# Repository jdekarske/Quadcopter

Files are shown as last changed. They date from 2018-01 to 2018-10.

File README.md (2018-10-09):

<<<<<<< HEAD
# README #

What a machine!

This REPO demonstrates the BADGER Lab's Motion Capture system applied to a 450mm quadcopter. The main interest to the lab is the integration of Optitrack Motive with MatLab. See the [documentation](https://v20.wiki.optitrack.com/index.php?title=Data_Streaming) for instruction on set-up. Download the NatNet SDK for use with MatLab. It should be set up on the lab computer, but I'm not sure if it applies to all user partitions. A MatLab example comes with the SDK.

## Quadcopter Usage
* Calibrate cameras liberally; ensure flight volume is thoroughly wanded and you receive an "exceptional" grade in all categories.
* Establish ground plane with the northwest corner of the forceplate.
* Line the quadcopter struts **EXACTLY** with the north end of the forceplate, motor one faces south.
* On GUI: ensure the rigid body moves with the correct axes, Frames per second match camera rate, abort button is greyed
* Start flight from hand, click motors on. Guide for a few seconds while the integral term catches up.

## Key Streaming Excerpts
* Initialize any variables under `function QuadcontrolV2_OpeningFcn(hObject, eventdata, handles, varargin)`
* The critical code comes from the initialization. Specify `addlistener( [rigidbody (probably '1')], [callback function])`.
```
c = natnet;
c.ConnectionType = 'Multicast';
c.connect
c.addlistener( 1 , 'ControlCallbackV2' );
```
* To grab position data in the callback, use the evnt structure. (Goodluck with the axes)
```
rbx = -double( evnt.data.RigidBodies( rbnum ).y );`
```
* Be sure to add buttons for `c.enable(0)` and `c.disable(0)` otherwise the script will not terminate and you will have to kill matlab via task manager and you'll be unhappy because you forget to do it properly after writing sticky notes to remind yourself.
* Use [set](https://www.mathworks.com/help/matlab/ref/set.html) and [drawnow](https://www.mathworks.com/help/matlab/ref/drawnow.html) functions for easy plotting and GUI stuff! *update: Don't use gui stuff while flying!! it adds significant computing time*

### Who should you contact when nothing works and is poorly commented?
[jdekarske@wisc.edu](mailto:jdekarske@wisc.edu?subject=Your%20code%20sucks)

*UW BADGER Lab 1/25/2018*
=======
# Quadcopter
Open-source flight controller software based on Optitrack position tracking
>>>>>>> Github/master

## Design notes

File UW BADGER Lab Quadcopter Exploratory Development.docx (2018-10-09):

# UW BADGER Lab Quadcopter Exploratory Development

Prepared by: Jason Dekarske 6/28/2018

# Abstract

A quadcopter is a study of the challenge of digital controls and its demand for well understood physics. Each component must work together flawlessly, or the consequences could be catastrophic. The goal of this project was to construct a custom 4 rotor robot capable of following high level commands from a command station using position input from the BADGER Lab’s motion capture system. The motivation is to create a testbed for student development in ME 349: Introduction to Robotics. We sourced inexpensive parts with the intention of creating more than one unit for the use in the course and to control for broken devices. This document outlines the progress made toward this goal and the things the author has learned.

# Note

This writing is organized by quad theory, then component functional discovery and finally system integration and theory. It is important to note that most components may not be available exactly as described, but it should be possible to find a clone for similar price range. With that said, the greatest difficulty was sidestepping physical properties of components, as documentation was scarce, and proceeding with experimentation and trial and error. Hopefully the strategies laid out are helpful in recreating a functional device in the case an exact replacement cannot be found.

# Wait, this thing flies?

There are many examples in literature that outline quadcopter function at the PhD level with formality that is not necessarily important to get this thing in the air. Alternatively, hobby documentation of open source flight computers cannot be made to meld with the unique setup in the BADGER Lab. This is precisely the challenge presented here. Where quadcopter research labs have thousands to produce a robust, acrobatic system (see: coding and algorithms), an introductory course that spends a small unit on flight cannot compete. This will be touched later in design criteria and some choices of subsystems.

With basic understanding of Newton’s laws, we can construct a working device that will (hopefully) not destroy itself. From this base we can add toppings that improve the flavor and robustness to the system. Every write-up on quadcopters must include a form of the following nifty graphic (Figure 1). Notice the body frame is attached in line with the rotors. This simplifies the math greatly, since a movement in one direction is only dependent on one axis. Additionally, adjacent rotors spin in opposite directions to cancel torque; we will abuse this later.

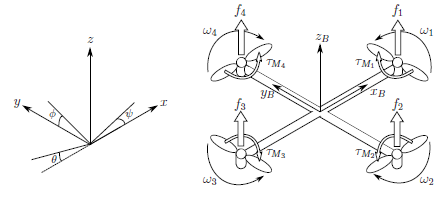
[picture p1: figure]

Let’s get some equations rolling. First, we will model the quadcopter attached to a vertical pole: controlling only its altitude (Excuse my janky powerpoint shape free body diagrams please).

M1,M2

M3,M4

mg

x

θ

After accepting the brutal truth that we will not have a perfectly stable quadcopter we would find it’s thrust to be the following:

T=∑ F_(Mi) *cosθ*cosφ-m*g

This means to accelerate up or down, we should modulate the force of the motors equally. Note the cosine terms include the angular correction for both horizontal axes. Not so tough, let’s look at keeping it stabilized. This time, we attach one axis to a horizontal pole (I actually did this, see later)

M1

M3

x

θ

In this plane, we are only looking at the rotational dynamics between opposite motors. We find the angular acceleration where I is the inertia of each axis and L is the length motor to motor (450mm):

I*θ=L/2(F_(M3) -F_(M1) )

I*φ=L/2(F_(M4) -F_(M2) )

Finally, we consider the final axis of the quadcopter: the yaw. Following a similar strategy, let’s only compare the relative forces of the motors.

M4

M2

M3

M1

As is the theme of this project, I was given no details of the physical properties of the propellers, so we need to take this part off-road a bit. We have intuition that rotating the M1,M3 pair faster than M2,M4 would result in the quad rotating clockwise (or negative Ψ) due to Newton’s second Law. If we assume the propellors are the same and everything is symmetrical, I conjecture:

IΨ=(F_(M2) +F_(M4) )-(F_(M1) +F_(M3) )

In the coming sections we will revisit how these physical relations can be put into code!

# I am in control!

Okay, so I’ve been pretty blunt about our lack of knowledge about our system. Surprise! Our engineering project isn’t ideal. The saving grace will be our controller, something that takes feedback from our sensors and adjusts accordingly. We’ll be using the popular PID scheme to correct errors. This requires an input, the motors, and an output, the position. This comes in two layers: stabilization and movement. Our inner layer, stabilization is priority number one. If we can keep the quadcopter stable, it ain’t goin nowhere. So, as our input, we command the angular position to be 0° for all axes. The controller will modulate the motors, as an output, to achieve this position with the help of the equations we developed earlier. Next, our outer later. Say we want to move our quadcopter 2 meters North (+y). Let’s command an angle ϕ = 2° and decrease to zero. This results in the quadcopter banking toward the north and stopping at 2 meters North. This all sounds good in theory, but let’s apply it.

I glossed over a crucial part of control in the last paragraph: PID. It stands for Proportional Integral Derivative, the three operations used in the algorithm. I’ll attack this in words and intuition first and equations after, feel free to switch between as you wish. These all work as a function of error, or the difference between the current input and the commanded input: e=z_0 -z , for example, where z is the height of the quadcopter and z_0 is our desired height of the quadcopter. Looking at the proportional term, it will take the error and multiply it by a “gain”, often k_p , and spit out an output, let’s say thrust. So, if we’re z=1 and want to be z_0 =3 , with k_p =2, T=2*(3-1)=4 . Our output thrust is 4 which commands the motors to spin faster and ascend. A little hand-wavy, I know, we will get to how “thrust” interacts with the motors. As the quad approaches our desired height, the error will decrease and thus, the thrust. However, if the quad is moving too fast as it gets to the desired path it may overshoot! We are higher than the desired point and the thrust goes negative, and the motors slow down to descend. Let’s fix this with the Derivative term. As the name implies, we take the derivative of the error, (de)/(dt) , so we need to factor in a time variable. Since a computer is doing this math, we’ll have discrete sample points to calculate the error and time between each sample, perfect! Let’s find the difference in error between now and the last sample and divide by the time it took. How does this help us? If we are approaching our desired height too fast we will notice a large negative derivative term, because the error is decreasing quickly. We multiply this by a term k_d and add it to the output. This decreases the output as we approach our desired point. Finally, we have the Integral term which is used for fixing steady state errors. The motors we have are quite sensitive, to stay within a ~cm of our setpoint, we need a low proportional term, or it will oscillate over and under the desired point. This is okay, but if the quad is very low, the term may not raise the output high enough to get to the desired point: a steady-state error. The integral term, as expected integrates, or adds, consecutive error between samples multiplies by the time between samples and you guessed it, k_I , and tacks it on to the output. In summary, P fixes error, I keeps P under control, and I fixes outstanding error. That was a lot, let’s put it in maths and grapths.

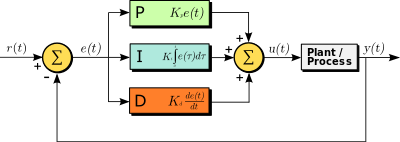
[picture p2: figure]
Image result for pid controller

Here we see the three familiar terms in the middle and a bunch of arrows pointing everywhere. r(t) is our desired point which stays the same, the summation circle subtracts the output, y(t) to give e(t), the error. Then, the PID terms do their thing and sum at the next circle to give our command to the motors, u(t). The motors move the quad, plant, and give us an output, position. Here are some examples of controllers with different gain values and how they interact. Note how red doesn’t overshoot, but it takes longer to reach the reference signal. These are the balances that must be made. Later we will work on finding what gains to use or “tuning”, this was the bulk of the time spent on the project.

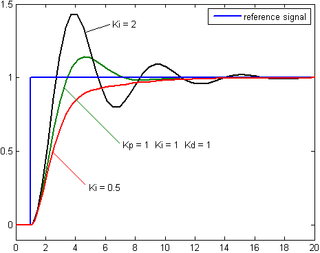
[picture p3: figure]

# Design criteria

Because this was meant for a near graduate level course, it’s important to make the system accessible for tinkering and experimentation in the scope of robotics. The following criteria are in no way absolute for professional, experimental, or hobby quadcopter design. Starting with the tinkering theme, we need a microcontroller that can talk to the motion tracking system and the motors: an Arduino is a cheap solution that is very easy to use. Next, a large quad can claim slower dynamics by its increased mass and rotational inertia. Additionally, a larger footprint gives us a larger margin of error for the tracking markers because they can be placed further apart. Human sized wouldn’t fit in the lab so we’ll go with a small dog sized craft. Typically, these come in the flavor of a 450mm wingspan and a kilo or two. Consequently, we’ll need bigger motors powered by a bigger battery. Finally, we need communication between all our systems. I would have liked to use wifi for everything, but IT has the building on lockdown for router paraphernalia. We’ll make our own radio signals with a common 2.4GHz RF transceiver (it’s faster than wifi anyway!). I’ll breakdown each component in the following subsections.

## Frame

Let’s start with the part that looks pretty and holds things together. It took two iterations before I decided to use a tried and true frame. The first was some plexiglass screwed together in a not so balanced way, so I could get a feeling for where the components could go. Initially, I chose an “H” configuration. This setup allowed me to use the full length of the board for mounting and routing wires. This came at a cost of added weight and asymmetrical inertias. I was embarrassed by my poor craftsmanship, so I moved on to round two.

From a salvaged plexiglass sheet found in the design scraps, (SE corner ECB basement, seriously, go there, it’s a goldmine) I laser cut a beautiful four-piece frame with splines and everything. It was taller and had a two-tier mounting area. The lower tier contained the battery to lower the center of gravity while the upper tier held the controller. This time I went with the “X” configuration. I figured that if I didn’t assign which way was forward, it’s easier to play coy when it doesn’t cooperate. Also, having a single motor assigned to each axis with similar inertias makes the math much easier. Finally, since I was constructing a 3-dimensional device from 2-dimensional pieces, having perpendicular intersections made fitting the pieces easier. My beautiful artwork met its fate when a motor failed, and it dive bombed the hardened concrete floor. Tears were shed, but it was best I moved on to something guaranteed by Amazon to work.

Here is the “RipaFire®” 450 frame that I found on Amazon that is surprisingly still sold more than a year later. It is even made of “advanced engineering material”! I chose this in particular because it had a built in power distribution board. The bottom part of the frame is actually a PCB which routes power from the battery to the ESC’s (covered later). This saves me an extra part and consolidates wires, always a plus. Additionally, the motors fit the standard holes at the ends, the battery can fit in the lower portion, and I have plenty of room for a microcontroller on top.

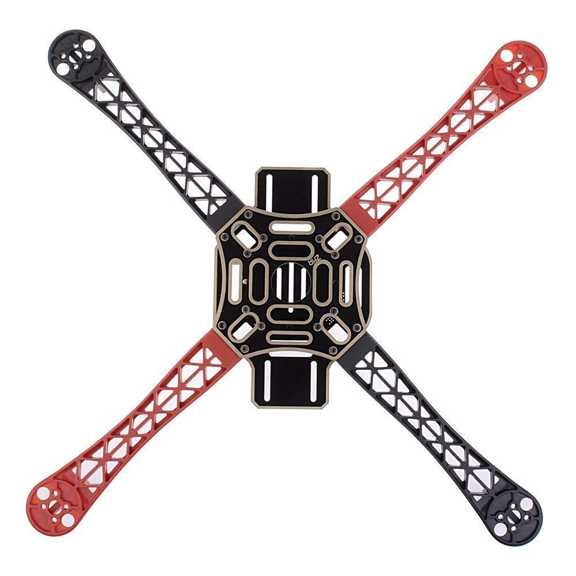
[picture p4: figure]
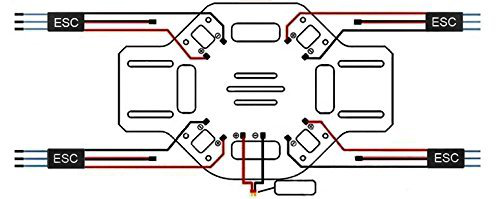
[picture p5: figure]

## Motors

On to the star players! This is what really drove the decision making for the other components. Without a huge background in aeronautics, I was stumped for what to choose. I had to stay away from quality genuine motors to save the budget so generic ones from AliExpress had to do. I scoured forums of custom builds to see what parameters were typical for a quad of my size. I settled on a 920KV brushless motor. KV is the velocity constant of the motor – thousand RPM/Volt. https://oscarliang.com/quadcopter-motor-propeller/ Generally, lower RPMs are suitable for larger propellers and quads. Since we have a rather large craft, I dutifully followed the table and stayed under 1000KV. When connecting to the ESC, the wires can connect in any combination; if the motor spins the wrong way, switch two of them.

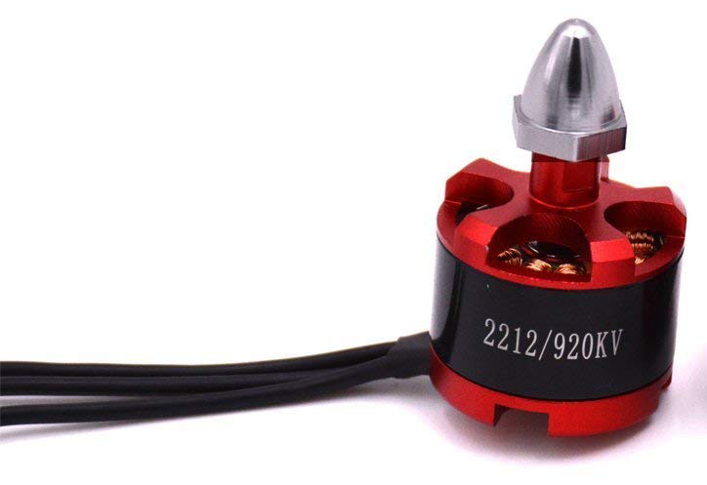
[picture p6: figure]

## Propeller

I’m not sure this deserves a section with how little I spent researching. In hindsight, one of the most critical features did not see that much love. They certainly showed their displeasure by providing several casualties to my defenseless fingers. Following the table from above, I used a 1045 propellor which means 10” diameter and 45° pitch. I ordered a few packs figuring these would break often, I was, unfortunately, very correct. We visited the direction these should spin earlier, double check, as these are directional.

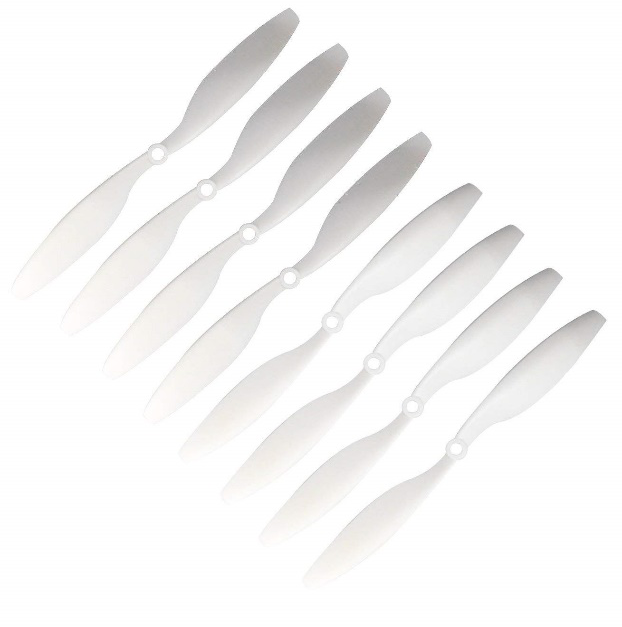
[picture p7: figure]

## Electronic Speed Controllers

What moves the motor you might ask? These convenient, drop and go, boards take PWM input from the controller and 12V from the battery, and transform to 3 phase output for the motors! Gorgeous! They just need a little programming. Most run with a standard firmware that is easy to change with an RC controller and a datasheet. The beauty of minimum spec designs meant I had neither! Fortunately, I could emulate a controller with the Arduino and after much experimentation with similar looking boards, I found a datasheet that kind of worked (See setup for details). The important parameter was finding an ESC with a high enough current rating. The only downside to choosing one with a higher rating meant a heavier piece. In this case, the weight of the ESC is negligible, so I went with a conservative 30A (compared to similar builds). Amazon gave me what I needed and a few extra after they burned out. I eventually found some that will cut the power if the motor stalls after getting the propellers caught under a desk. This and other features will be explored later. Note the extra is the output of the battery elimination circuit (BEC) which powers our microcontroller with a nice 5V.

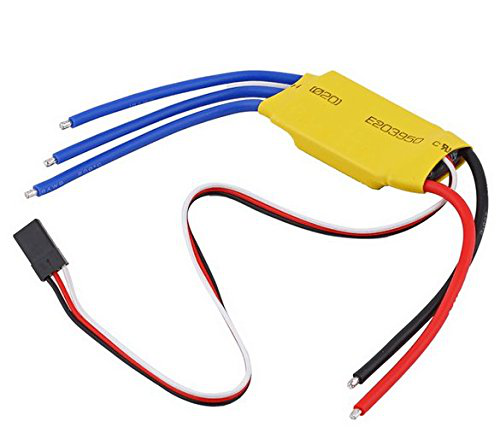
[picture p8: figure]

## Battery

Going down the line we see the heaviest chunk in the mix. The 4 cell LiPo was chosen based on reviews from Amazon and requirements for the motors capabilities. Out of all the parts, this is potentially the most dangerous. Starting Peter’s lab on fire was pretty high on the list of “do not’s”. I also grabbed a charger with a balancing feature. It’s crucial to note the cells should not be discharged lower than 3V. I tested the battery before and after sessions and when it was clear the motors weren’t working as hard as usual. The battery needed a discharge rate that would match our use. The “C” rating determines the nominal current available. With a 2.2 Ah capacity and 25C rating, our available current is 2.2*25 = 55A. This means it should be tough to burn out our ESC’s at full power when the current is distributed to four motors.

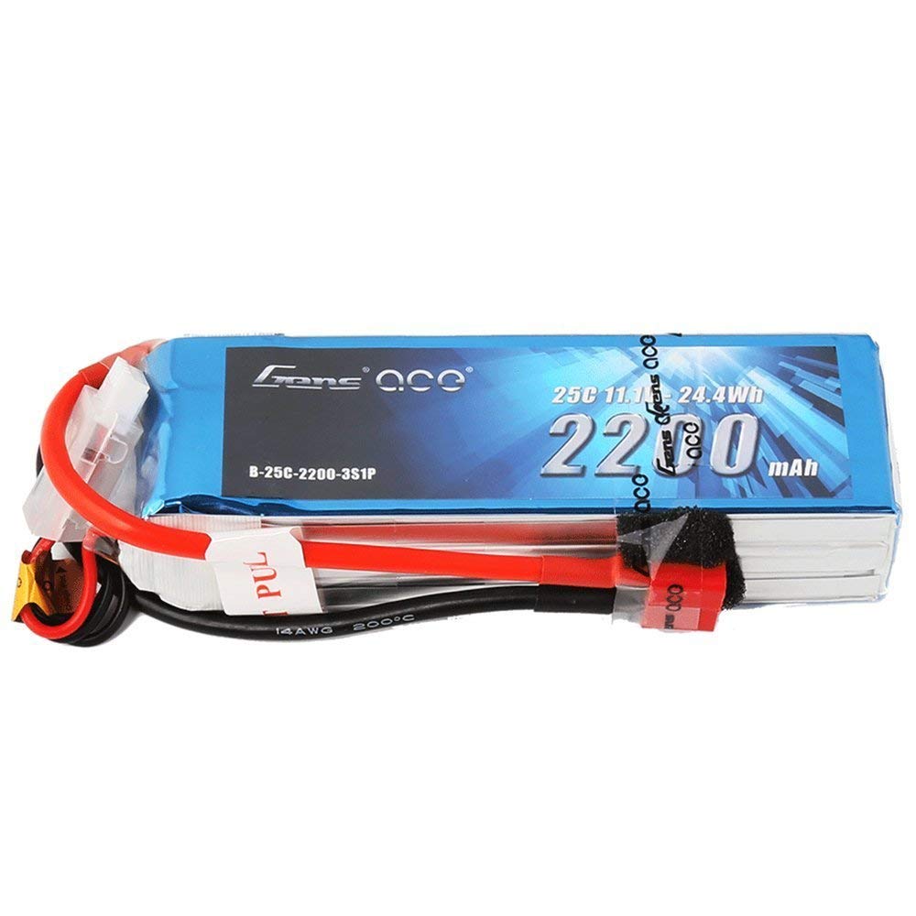
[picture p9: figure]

## Microcontroller

Being well versed in the language of DIY made this an easy choice. I needed 4 PWM channels, serial, SPI and I²C support, 5V power, and be on the small side. I already used an Arduino in tandem with the NRF24L01 (next section!) so implementation would be quick, or so I thought. I went with a clone of an Arduino Nano, fairly small, and it hits all the requirements.

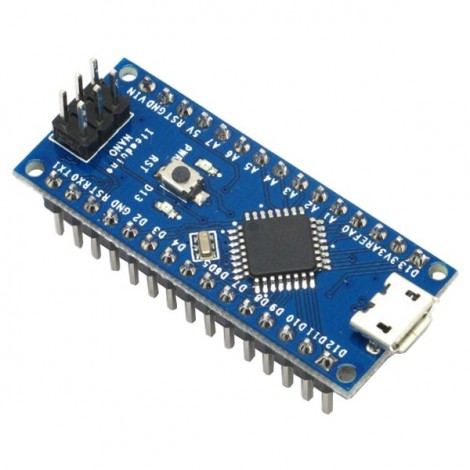
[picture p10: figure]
Image result for arduino nano clone

## RF Transceiver

This choice was part necessity, part personal preference. Like I said before, I knew wifi communication would be a battle I didn’t want to fight with IT so I sprung for the next best option. The NRF24L01 is a popular chip used by many hobbyists because of an extremely well documented and supported library for Arduino. I could have chosen Bluetooth, which is similar but I didn’t need to worry about acknowledgements or connection testing, so I threw that all out. I could easily send a string to be parsed on the other side with a simple function. The commands moved so fast, it wasn’t worth checking if they got there as a new command was already on its way. The only modification was a 47 uf decoupling capacitor soldered between power and ground.

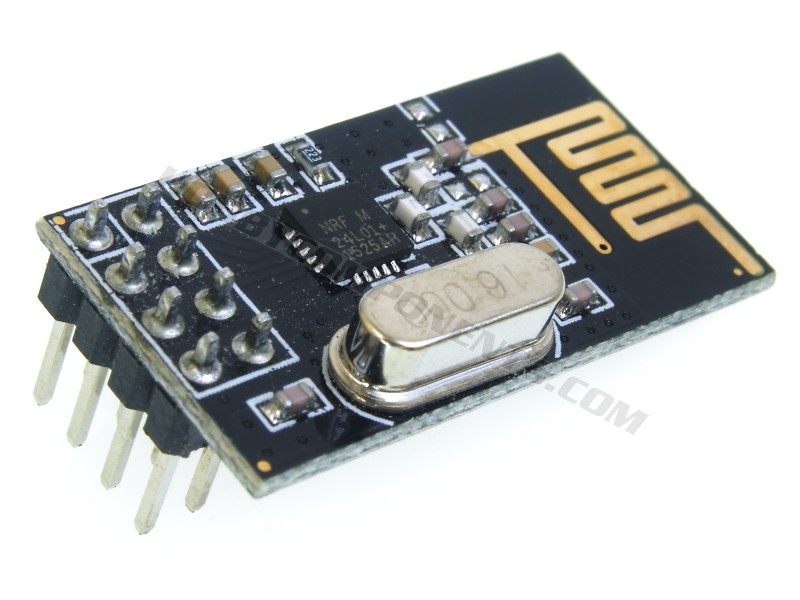
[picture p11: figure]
Image result for nrf24l01

## PCB

The electronic glue that replaced my rats nest of a protoboard. Although wire wrapping is a great step up from breadboard prototyping, it doesn’t stand a chance against a perfectly (maybe) printed board. I discovered my digital signals just weren’t clean enough for clean handling. I began my trial by fire with Altium and found it wasn’t too bad (with a few components that is, the coals are burning my feet with my current project). I tried using the OtherMill at the makerspace to make my own, but they wouldn’t order double-sided boards for some reason. Forever a grudge I’ll hold. I sent my gerber files to the first search result which offered 5 boards for $20. I believe Osh Park is cheaper for one board, but hey, now we have 5. I included space for an RGB Led if you so wish. You’ll find them here https://www.adafruit.com/product/314 or from Mike. You’ll find the files in the repo.

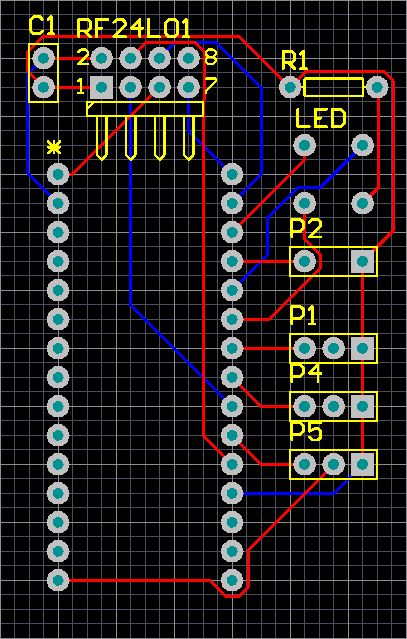
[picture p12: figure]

## Inertial Measurement Unit

Although not actually used, I do have one mounted on the frame and connected to the Arduino (the frame had a pair of screws that conveniently matched the breakout). I wanted to solely use the camera system for measurement, but the system could be completely robust if included. The cameras max out at 240Hz and there will be a delay through the system reaching the motors. The IMU on the other hand samples at 1000Hz and skips the lengthy communication gaps. With more time I would’ve introduced a stabilization inner loop with the IMU and a position control outer loop with the camera system. I have an MPU6050 breakout which communicates via I2C. Hopefully whoever is reading this can take on that challenge.

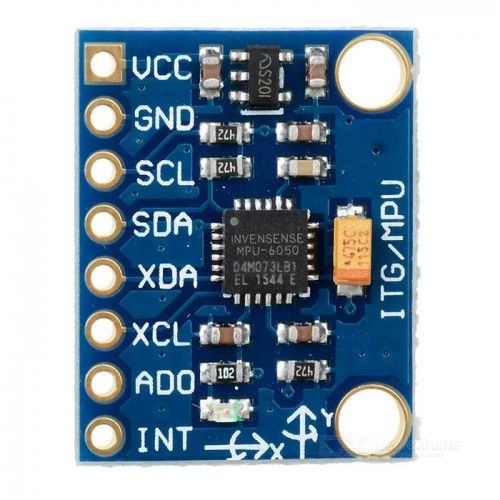
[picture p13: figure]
Image result for mpu6050

# Let’s count how many comments are in my code.

## Arduino

## Matlab

# “Figuring things out”

Let’s get down to business. I’ll be running though my workflow of tinkering with the various components.

ESC

Motor calibration curve

inertia

# Just make it fly already.

The following is a checklist I would run each time I began a session:

1. Setup motion capture
  a. Change all the cameras to 100Hz to match the matlab script.
  b. Hide all IR balls in the room and run the usual BADGER Lab calibration protocol with cameras focused on the flight area. I liked to use the forceplates as the ground plane as those are closest to level.
  c. On the streaming tab, enable and ensure axes match those in the matlab script. The status indicator on the lower left should be yellow (or green if matlab is taking streaming data).
  d. Add about 7 IR balls to the quad in an asymmetrical arrangement.
  e. Position the quad on the forceplate with the legs exactly along the length. This ensures the quad axes are aligned directly with the motors. (picture)
  f. Add as a rigid body (I don’t think it has to be named anything, leave it as the default).
2. Quadcopter
  a. Ensure battery is fully charged (12.6V).
  b. If desired, attach killswitch string to battery connector and wrist (proved successful multiple times).
  c. Plug in battery and wait for happy chime sequence, all motors should sound in unison, swap around ESC’s and motors to troubleshoot.
  d. Ensure propellers are screwed tight.
  e. Plug in homebase Arduino via USB.
3. Matlab
  a. In quad control callback check that framerate matches Motive.
  b. Run quadcontrolV4
  c. The GUI has been disabled to cut a ridiculous amount of latency. (future work: update every second or two rather than every frame. Or threading if you’re ambitious)
  d. Close the window and reopen to load the serial ports (bug) and choose the one connected to the home base Arduino
  e. With the quad battery unplugged, click “motors on” and move the quad manually to ensure the axes are correct and the motor commands react appropriately. You may have to add some print commands.
  f. The script should abort if the quad falls too low or rotates too extreme, you may test that now.
  g. With the script in “abort mode” plug in the battery and hold the quad in outstretched hand with sleeves and safety glasses on. Click “motors on”
  h. Guide the quad until the integral term catches up and provide small bumps to keep it on track. Soon you’ll start to feel cool powers where you think you can tune it by hand and spend an entire year doing so. Good luck!

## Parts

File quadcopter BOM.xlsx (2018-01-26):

Item | Quantity | Cost | Quantity in use
Arduino Nano | 3 | 11.86 | 2
1045 Propellors (keyed shafts) | 8 | 10.99 | 4
3S JST-XH Battery Balance Connector Plug Adapter 15CM | 10 | 6.99 | 1
1045 Propellors (nonkeyed shafts) | 16 | 13.99 |  | Wrong kind of shafts couldn’t return :(
WOAFLY 2212 920kv Brushless Motor | 4 | 34.99 | 4
30A Brushless Motor Speed Controller RC BEC | 4 | 39.6 | 4
F450 4-Axis Multi-Rotor Quadcopter Frame | 1 | 19.99 | 1
iMAX B6AC Version 2 Digital LiPo LiIon LiFe NiMH NiCd 2S 3S 4S 5S 6S RC Battery Balance Charger and Discharger with DC PC USB Port Temperature Port | 1 | 54.99 | 1
Gens ace LiPo Battery Pack 2200mAh 25C 3S 11.1V with Deans Plug | 2 | 31.98 | 2
 |  | 225.38

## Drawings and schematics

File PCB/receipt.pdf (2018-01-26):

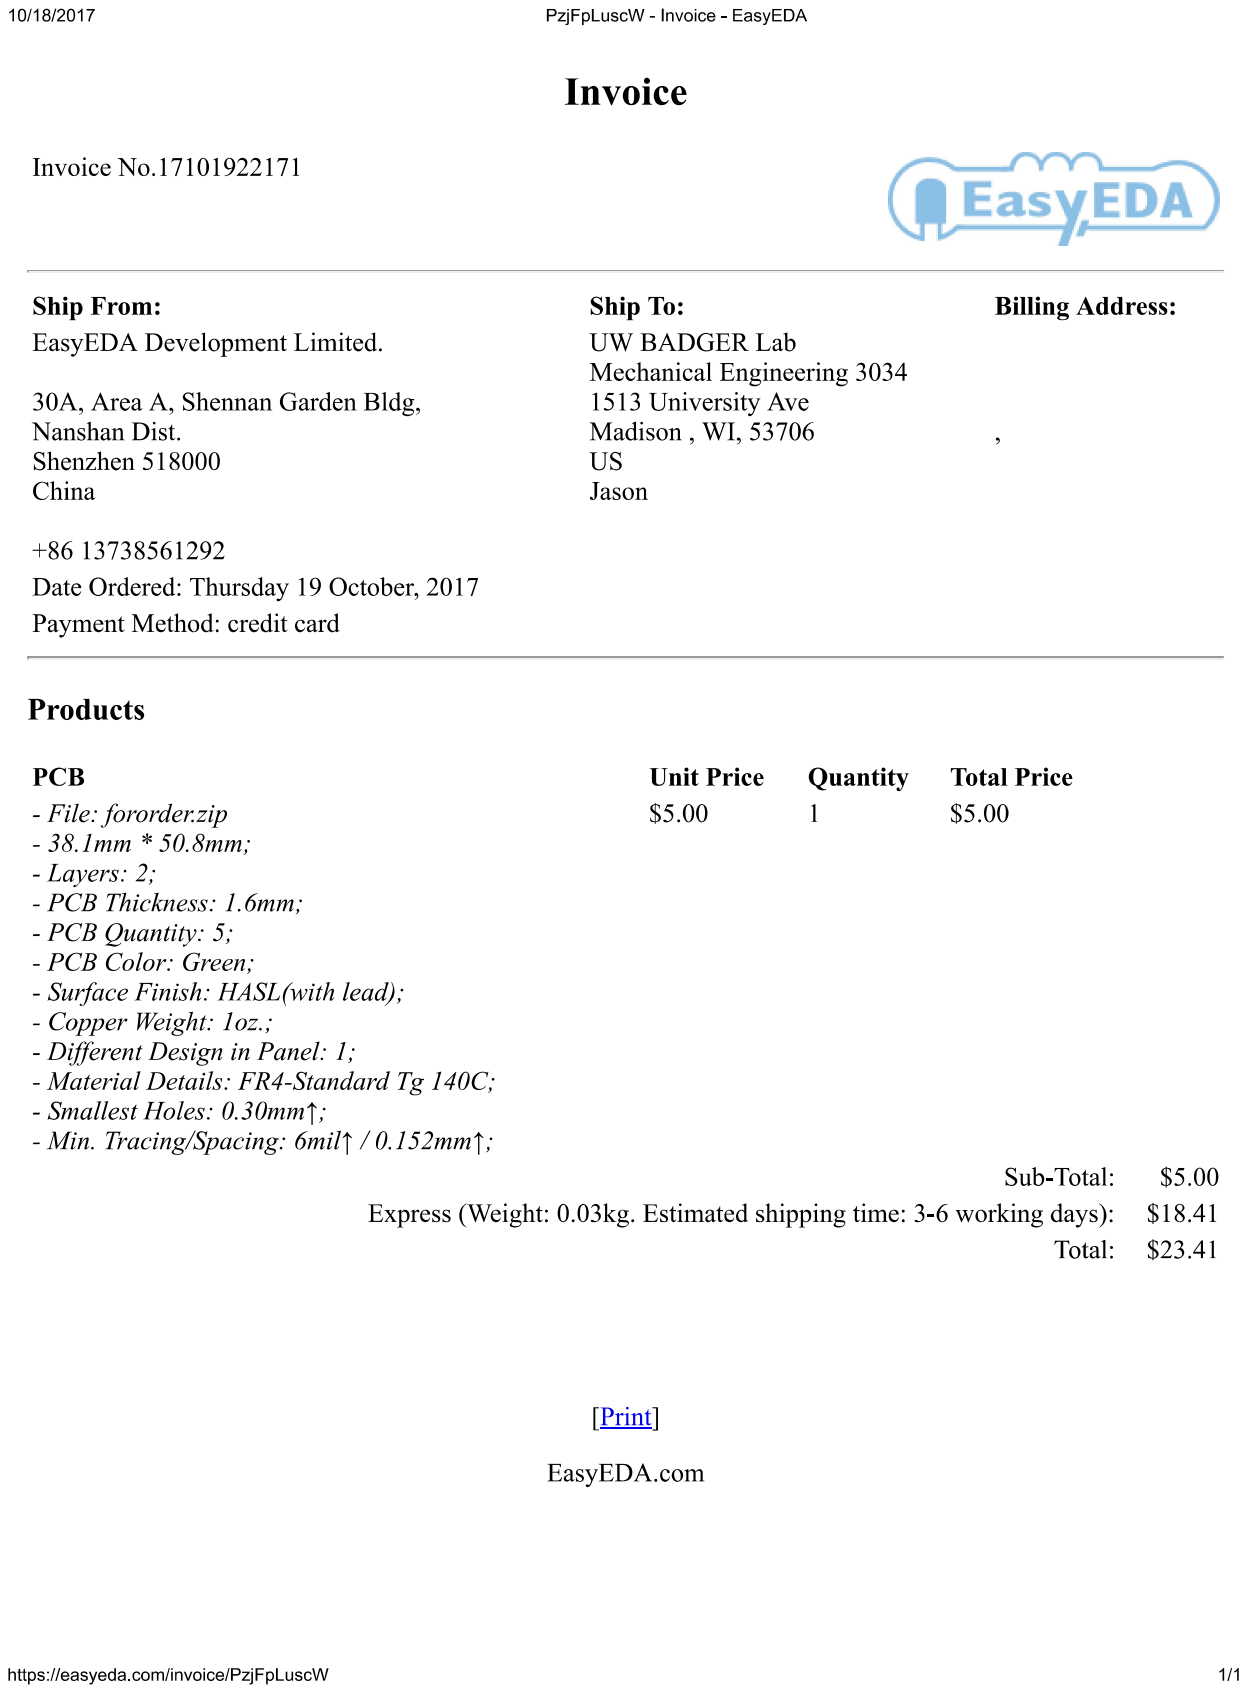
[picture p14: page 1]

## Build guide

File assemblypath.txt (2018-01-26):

D:\Motive Streaming to Matlab\NatNetSDK\Samples\bin\NatNetML.dll

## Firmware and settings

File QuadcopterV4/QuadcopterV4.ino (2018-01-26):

/*
Jason Dekarske
This version attempts to control individual motors
TODO:
parseInt alternative
radio.writefast
error checking ...I did some in Matlab
*/

#include <SPI.h>
#include "RF24.h"
#include <Servo.h>

/*************** For Timing Things ************************/
long now;
/**********************************************************/


/********************* Config *****************************/
/* 1 is transmitter module, 0 is quadcopter */
bool radioNumber = 1;
/* Set up radio on pins 7 and 8 for CE,CS */
RF24 radio(4,2);
byte addresses[][6] = {"1Node","2Node"};
/* Motors */
Servo e1, e2, e3, e4;
int m1, m2, m3, m4;
char beginchar; //stores motor delimiter
struct payload {
  int m1 = 0;
  int m2 = 0;
  int m3 = 0;
  int m4 = 0;
};
int gpin = 4;
int bpin = 10;
int rpin = 2;
float battery = 0.0;

/**********************************************************/
char buff[3];
char rec;
int readSerial(){
    for (int i=0; i<4; i++) {
      rec = Serial.read();
      buff[i] = rec;
    }  
  return(atoi(buff));
}

void setup() {
  Serial.begin(115200);
  e1.attach(3);
  e2.attach(5);
  e3.attach(6);
  e4.attach(9);
  e1.writeMicroseconds(1000); //Start with low speed in case they were left on
  e2.writeMicroseconds(1000);
  e3.writeMicroseconds(1000);
  e4.writeMicroseconds(1000);
  Serial.println("Layout:");
  Serial.println("1        2"); //may not be right
  Serial.println("|        |");
  Serial.println("+--------+");
  Serial.println("|        |");
  Serial.println("4        3");
/***************** Battery Stuff **************************/

  now = micros();
  pinMode(gpin, OUTPUT);
  pinMode(bpin, OUTPUT);
  pinMode(rpin, OUTPUT);

/**********************************************************/  
  radio.begin();
  //RF24_PA_MAX is default. Change with power issues
  radio.setPALevel(RF24_PA_LOW);
  
  // Open a writing and reading pipe on each radio, with opposite addresses
  if(radioNumber){
    radio.openWritingPipe(addresses[1]);
    radio.openReadingPipe(1,addresses[0]);
  }else{
    radio.openWritingPipe(addresses[0]);
    radio.openReadingPipe(1,addresses[1]);
  }

  // Start the radio listening for data
  if(radioNumber){
    radio.stopListening();
  }else{
    radio.startListening();
        e1.writeMicroseconds(1000);
        e2.writeMicroseconds(1000);
        e3.writeMicroseconds(1000);
        e4.writeMicroseconds(1000);
  }
  //radio.enableDynamicAck(); //We don't need acknowledged packets...we wanna go FAST
  //radio.setAutoAck();
  Serial.println("Ready! Control speed with 1000-2000");
}

void loop() {
  
/****************** Transmitter ***************************/  
if (radioNumber == 1)  {
    
    if(Serial.available() >= 17){ //look for start character, take 4 motor speeds, dump the rest
      //now = micros();
      beginchar = Serial.read();
      if(beginchar == 'a'){    
        payload speeds; 
        speeds.m1 = readSerial(); //This should be improved 
        speeds.m2 = readSerial();
        speeds.m3 = readSerial();
        speeds.m4 = readSerial();
        //while(Serial.available() > 0) { //clear out serial buffer just in case, this might be screwing up the buffer, consider adding newline tag
        //  Serial.read();
        //}
        Serial.print("Now sending: ");
        Serial.print(speeds.m1);
        Serial.print(", ");
        Serial.print(speeds.m2);
        Serial.print(", ");
        Serial.print(speeds.m3);
        Serial.print(", ");
        Serial.println(speeds.m4);
        if (!radio.write( &speeds, sizeof(payload))){    
          Serial.println("failed");
        }else{
          //Serial.println(micros()-now);
        }
      }
    }
  }

/****************** Quadcopter ***************************/

  if ( radioNumber == 0 )
  { 
      while (radio.available()) {                                   // While there is data ready      
        payload speeds;
        radio.read( &speeds, sizeof(payload) );
        e1.writeMicroseconds(speeds.m1);
        e2.writeMicroseconds(speeds.m2);
        e3.writeMicroseconds(speeds.m3);
        e4.writeMicroseconds(speeds.m4);
      }
//      if (micros()-now >= 5 * 1000000){ //check battery every 5 seconds
//        //battery = analogRead(A4) * 4.75*3/1024.0;
//        Serial.println(battery);
//        now = micros();
//        if (battery > 11.75){
//          digitalWrite(gpin, HIGH);
//        }
//        else if (battery > 11) {
//          digitalWrite(bpin, HIGH);
//        }
//        else if (battery > 10) {
//          digitalWrite(rpin, HIGH);
//        }
//        else {
//        while(1){//battery error
//          e1.writeMicroseconds(1000);
//          e2.writeMicroseconds(1000);
//          e3.writeMicroseconds(1000);
//          e4.writeMicroseconds(1000);
//          digitalWrite(rpin, HIGH);
//          delay(100);
//          digitalWrite(rpin, LOW);
//          delay(100);
//          if ((analogRead(A4) * 5/1024.0)>1){
//            break;
//          }
//        }
//      }
//
//
//      }
//      if (micros()-now >= 2.5 * 1000000){ //threading the led
//        digitalWrite(gpin, LOW);
//        digitalWrite(bpin, LOW);
//        digitalWrite(rpin, LOW);   
//      }

 }
 
} 

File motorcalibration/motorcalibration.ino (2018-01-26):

#include <Servo.h>


long value = 0; // set values you need to zero
long val = 0;

Servo e1, e2, e3, e4; //Create as much as Servoobject you want. You can controll 2 or more Servos at the same time

void setup() {
  
  pinMode(LED_BUILTIN, OUTPUT);
  Serial.begin(9600);    // start serial at 9600 baud
  e1.attach(3);    // attached to pin 9 I just do this with 1 Servo
  e2.attach(6);
  e3.attach(5);
  e4.attach(9);
  digitalWrite(LED_BUILTIN, HIGH);
  e1.write(2000);   //throttle high
  e2.write(2000);
  e3.write(2000);
  e4.write(2000);
  delay(10000);
  e1.write(1250);   //throttle low
  e2.write(1250);
  e3.write(1250);
  e4.write(1250);
  delay(3000);  

}

void loop() {

//First connect your ESC WITHOUT Arming. Then Open Serial and follo Instructions
 
  e1.writeMicroseconds(value);
  e2.writeMicroseconds(value);
  e3.writeMicroseconds(value);
  e4.writeMicroseconds(value);
  delay(15);
  if(Serial.available()) 
    val = Serial.parseInt();    // Parse an Integer from Serial
    value = map(val, 0, 100, 1250, 2000);

}
